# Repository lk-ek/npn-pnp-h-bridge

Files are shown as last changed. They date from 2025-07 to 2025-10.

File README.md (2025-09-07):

# H-Bridge Driver for 3.3V PWM Input (HI/LO)

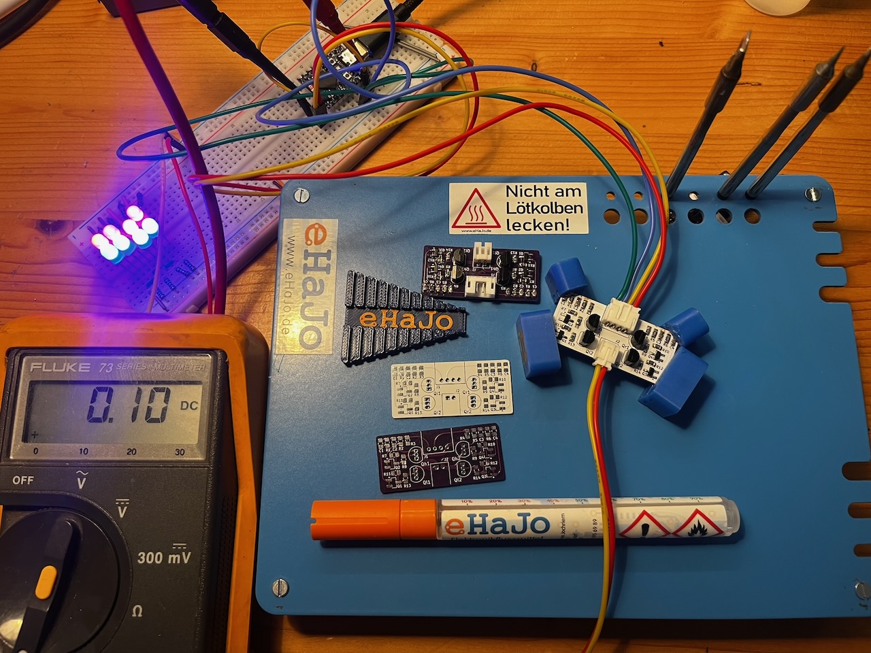
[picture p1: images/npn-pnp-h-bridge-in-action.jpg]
NPN-PNP-H-Bridge-in-action


This project is a discrete transistor-based H-bridge driver designed to drive loads such as a bi-directional LED string or small DC motors (you *need* to populate the protection diodes in that case!) using two 3.3V logic-level PWM inputs.

Special thanks to [PCBWay.com](https://pcbway.com) for reaching out to supply me with prototype PCBs. They turned out amazing and do work like a charm! This gave me the opportunity to fix a few things I got wrong in the first version - especially adding the protection diodes so this circuit can now not only drive LED-strips with anti-parallel circuits, but also small DC motors.

Also, if you are looking for a tool to handle your PCBs while soldering, look no further - [eHaJo's LötDock](https://www.ehajo.de/products/lotdock-workshop-set-a5-lotdock-base-a5-lotdock-starterkit) is there to save you! It's awesome. See it in action for a minute [here](https://www.youtube.com/watch?v=5W0FboXXDTc) (timelapse of the assembly of this PCB).

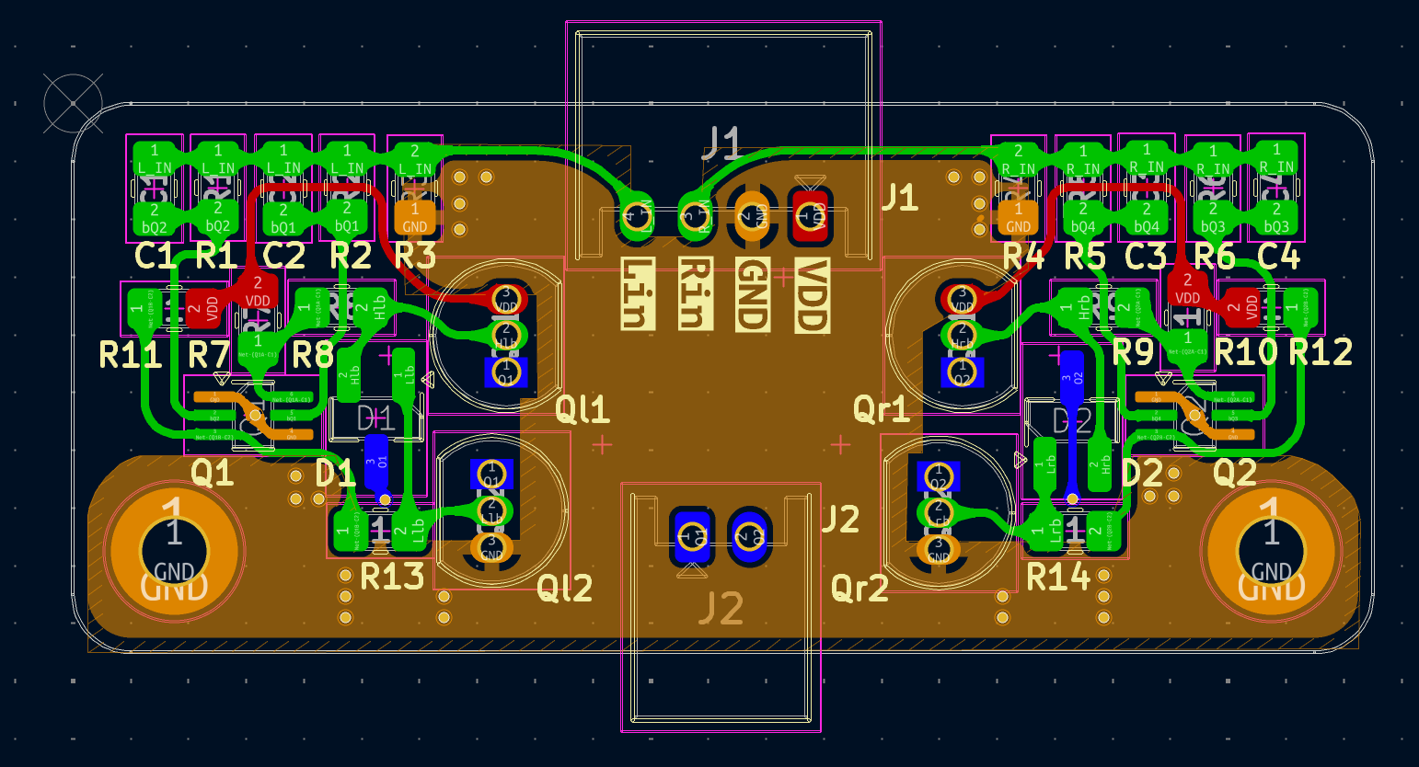
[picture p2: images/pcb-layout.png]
PCB Layout Front

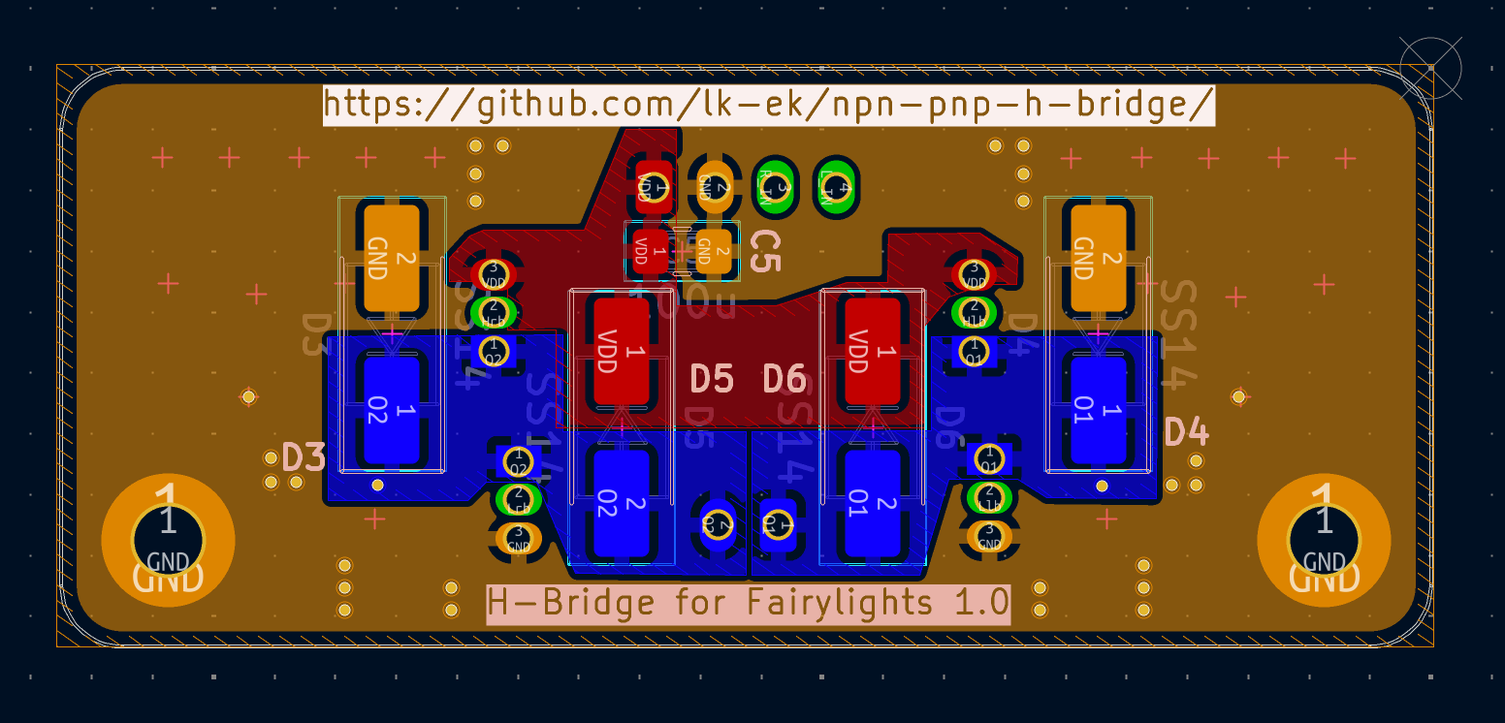
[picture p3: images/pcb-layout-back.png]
PCB Layout Back

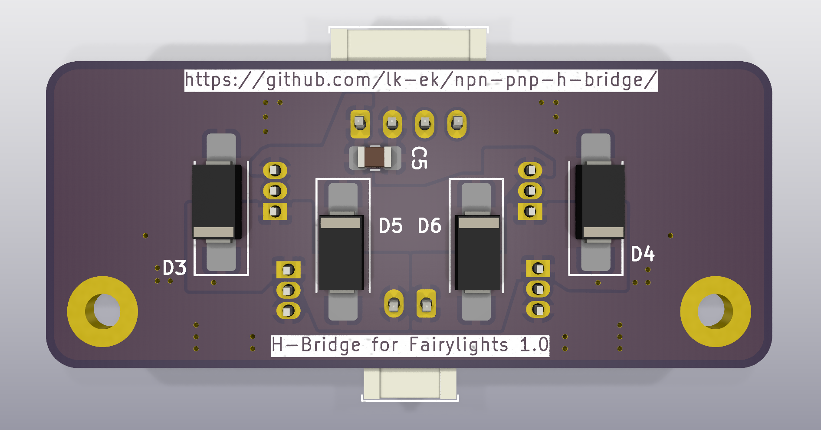
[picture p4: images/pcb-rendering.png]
PCB Rendering front

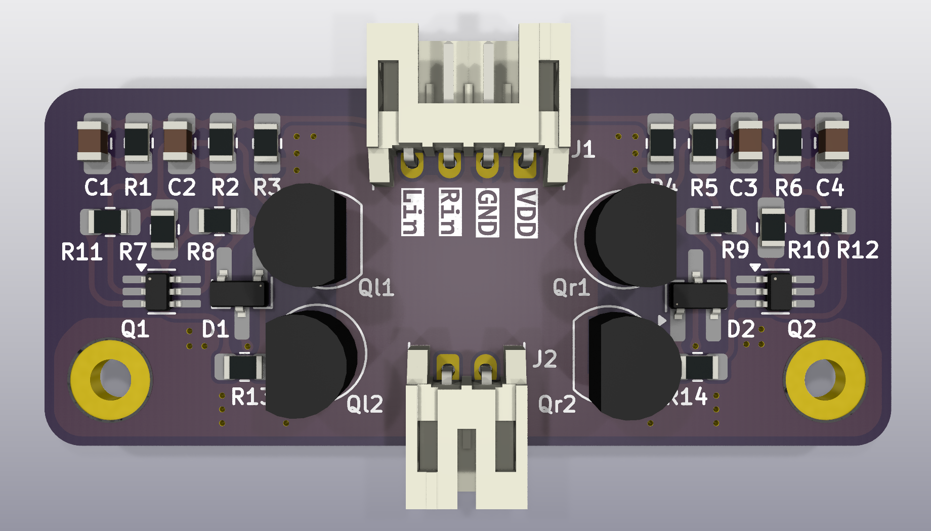
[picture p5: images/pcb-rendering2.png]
PCB Rendering back

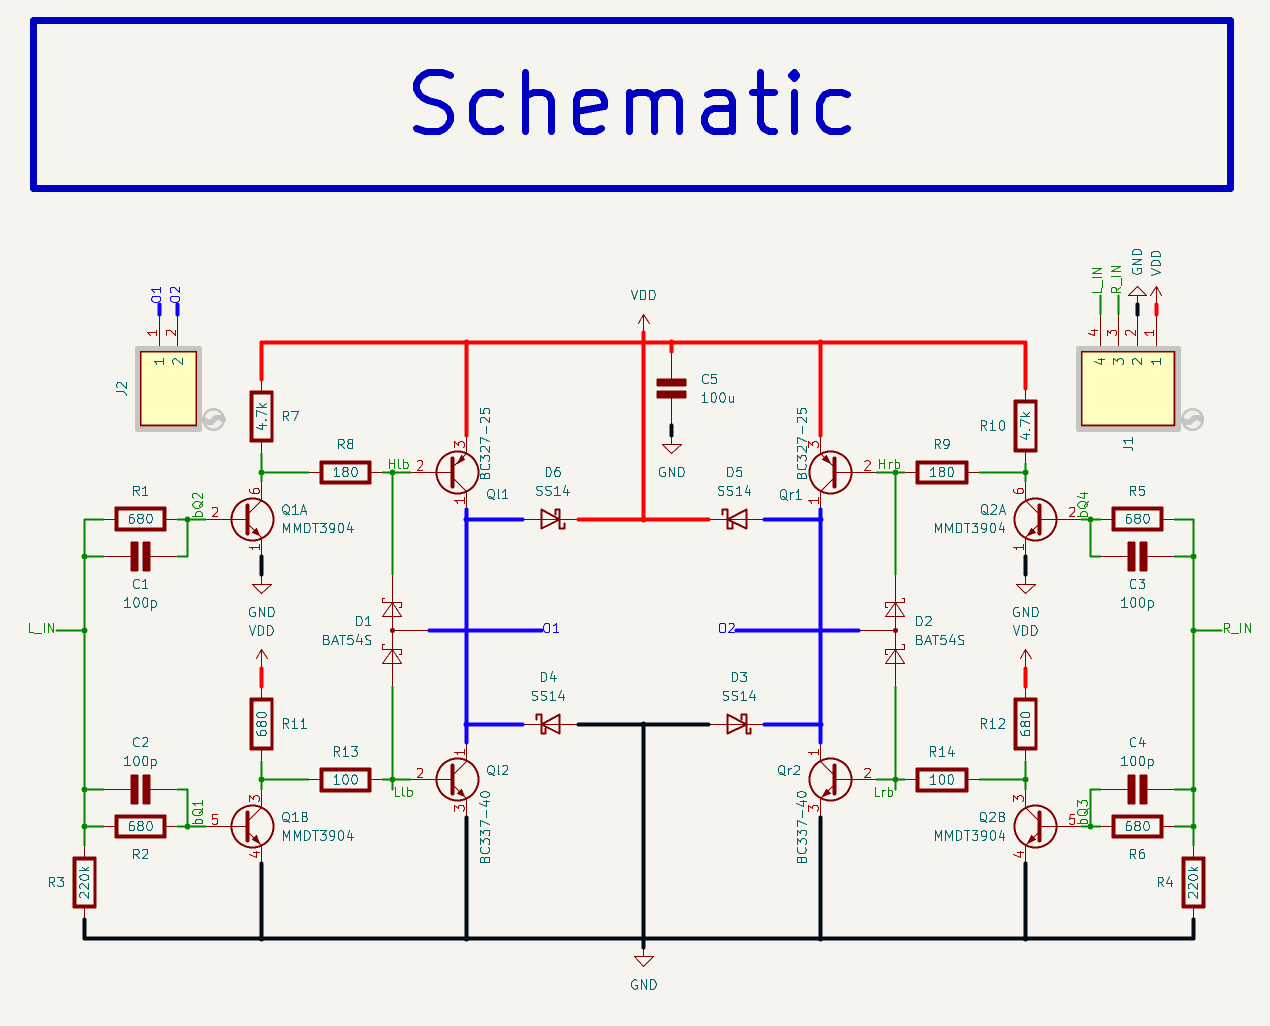
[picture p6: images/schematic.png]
Schematic


## Overview

The circuit takes two complementary (non-overlapping) PWM inputs: `L_IN` and `R_IN`, each at 3.3V logic level. These signals are level-shifted and drive a discrete H-bridge output stage composed of NPN and PNP BJTs. The output connects to a load (e.g., LED strip) in a push-pull fashion.

## Inputs

- `L_IN`: 3.3V logic PWM input (controls left-side NPN-PNP transistors)
- `R_IN`: 3.3V logic PWM input (controls right-side NPN-PNP transistors)

⚠️ **Important:**  
`L_IN` and `R_IN` **must be phase-shifted**, even though the NPN-PNP-pair makes sure shoot-through is impossible. If both are high simultaneously, the output is off.

## Supply

- `VDD`: Power rail for the H-bridge (used to drive the load), probably up to 12V
- `GND`: Common ground

## Outputs

- `O1`, `O2`: Differential outputs to the load

## Notes

- Input resistors and capacitors are used for filtering and protection.
- BJTs are used in complementary pairs (NPN/PNP) for each half-bridge.
- The BAT54S dual-diodes serve as a baker clamp to help the BJTs switch faster and reduce shoot-through from 2-3us to 0.5us in the simulation
- So far, a one-sided load of 210mA worked fine without anything getting noticably warm. In theory, it should tolerate at least 250mA on each side of the H-Bridge, so at least 500mA in total, but this is so far untested.
- Load: connected between `O1` and `O2` (e.g., antiparallel LEDs or small DC motor)
- You can use [WLED](https://kno.wled.ge/) to drive the inputs - select "PWM CCT" as LED-type. For the phase-shifted PWM to work, you might need to use a beta version from [wled-install.github.io](https://wled-install.github.io/) - 0.16 nightly worked for me.  
- [ESPHome](https://esphome.io) works as well, see example below

```yaml
output:
  - platform: ledc
    id: pwm_l
    pin: 3
    frequency: 5kHz
    inverted: false
    phase_angle: 0.0

  - platform: ledc
    id: pwm_r
    pin: 4
    frequency: 5kHz
    inverted: false
    phase_angle: 180.0

  - platform: template
    id: pwm_bridge
    type: float
    write_action:
      lambda: |-
        float duty = clamp(state, 0.0f, 1.0f) * 0.5f;
        id(pwm_l).set_level(duty);
        id(pwm_r).set_level(duty);
        ESP_LOGD("custom", "H-Bridge Control: L=%.2f R=%.2f", duty, duty);
light:
  - platform: monochromatic
    name: "Bidirektionale Lampe"
    output: pwm_bridge

```

## Simulation

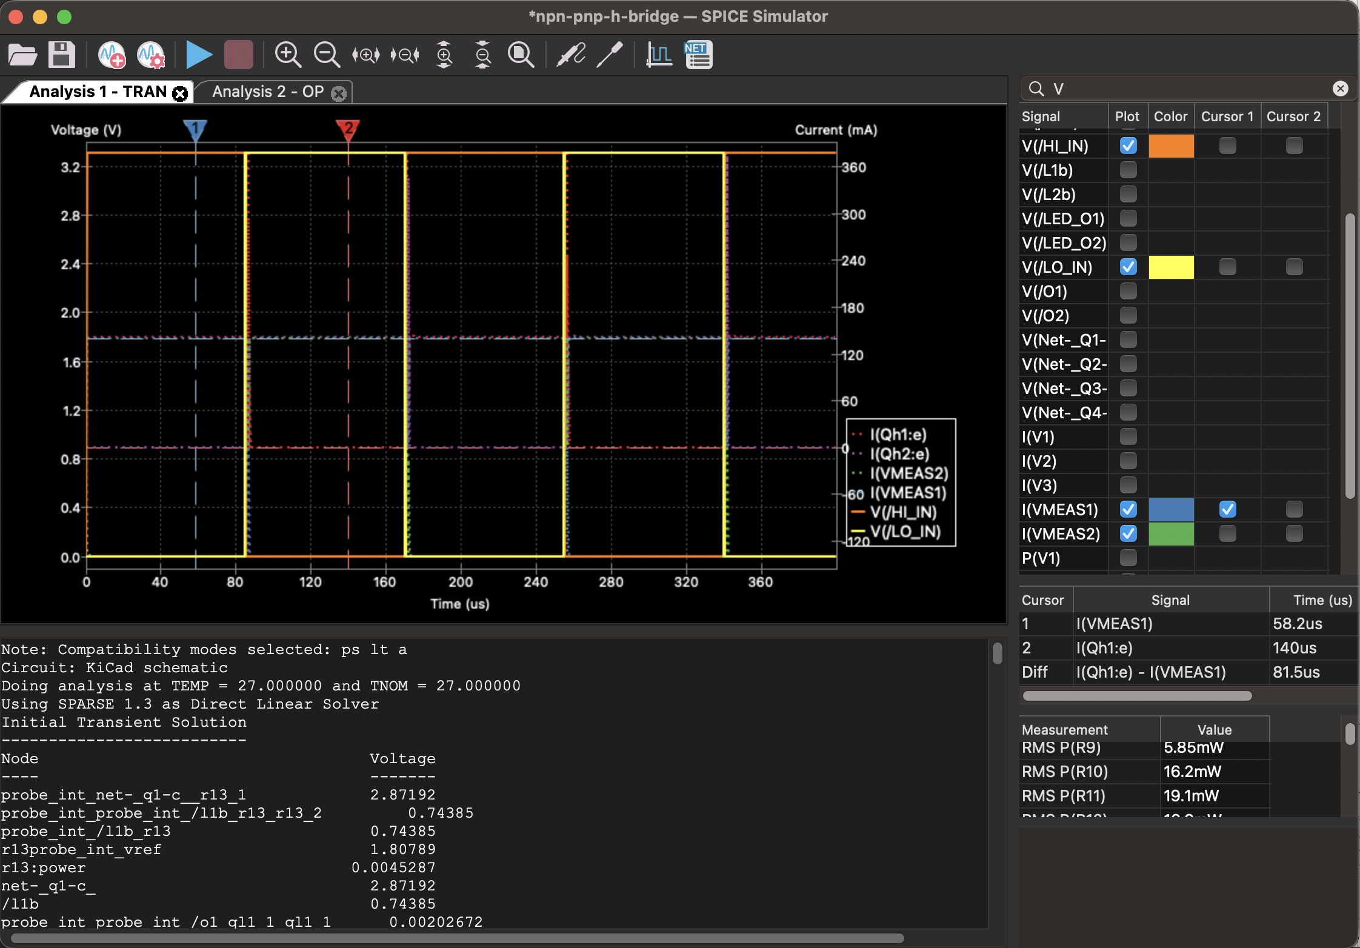
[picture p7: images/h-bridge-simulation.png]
H-Bridge Simulation

You can use KiCad's simulation tool to simulate the behaviour of this schematic. Modify the parameters of V1 and V2 to simulate different PWM patterns.

## Gerber files

You can download the gerber file directory as a zipfile and directly upload it to e.g. https://aisler.net, https://jlcpcb.com or https://pcbway.com

[Gerber file directory](production/npn-pnp-h-bridge)

## BOM

View [interactive BOM here](https://lk-ek.github.io/npn-pnp-h-bridge/)

| Designator | Amount | Value | Package |
|---|---|---|----|
| C1, C2, C3, C4 | 4 | 100p | 0805 
| C5 | 1 | 100u | 0805 
| D1, D2 | 2 | BAT54S Dual Schottky Diode | SOT-23 |
| D3, D4, D5, D6 | 4 | SS14 Schottky Diode | SMA |
| J1 | 1 | JST S4B-PH-K-S | JST PH 2.0mm |
| J2 | 1 | JST S2B-PH-K-S | JST PH 2.0mm |
| Q1, Q2 | 2 | MMDT3904 Dual NPN Package | SOT-363 |
| Ql1, Ql2 | 2 | BC327-25 | TO-92 |
| Qr1, Qr2 | 2 | BC337-40 | TO-92 |
| R1, R2, R5, R6, R11, R12 | 6 | 680 | 0805 |
| R3, R4 | 2 | 220k | 0805 |
| R7, R10 | 2 | 4.7k | 0805 |
| R8, R9 | 2 | 180 1/4W | 0805 |
| R13, R14 | 2 | 100 1/4W | 0805 |

## License

Attribution-NonCommercial-ShareAlike 4.0 International

See LICENSE for details, or: https://creativecommons.org/licenses/by-nc-sa/4.0/

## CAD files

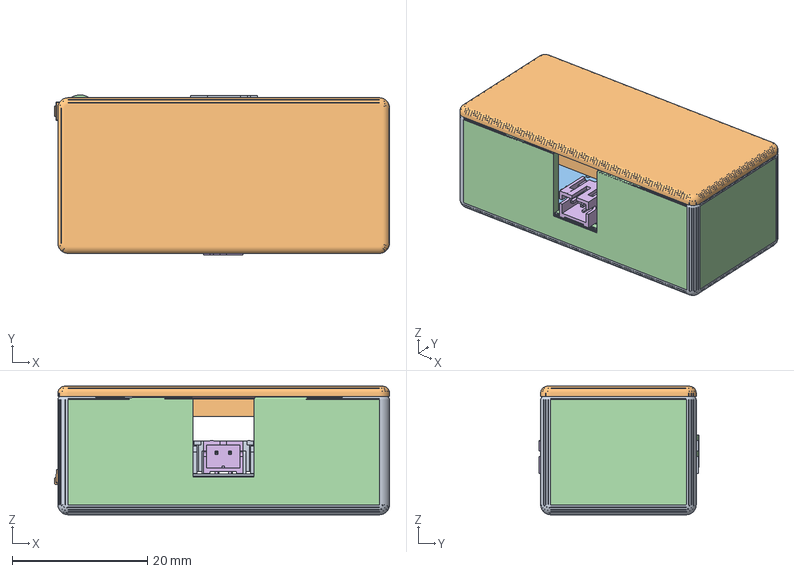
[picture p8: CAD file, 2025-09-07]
case/Test2.FCStd
49.5 x 23.7 x 19.0 mm
Deckel
C_0805_2012Metric
TO-92_Inline
R_0805_2012Metric
JST_PH_S2B-PH-K_1x02_P2.00mm_Horizontal
SOT-23
SOT-363_SC-70-6
JST_PH_S4B-PH-K_1x04_P2.00mm_Horizontal
D_SMA
npn-pnp-h-bridge_PCB
Body (Meshed)
Deckel (Meshed)

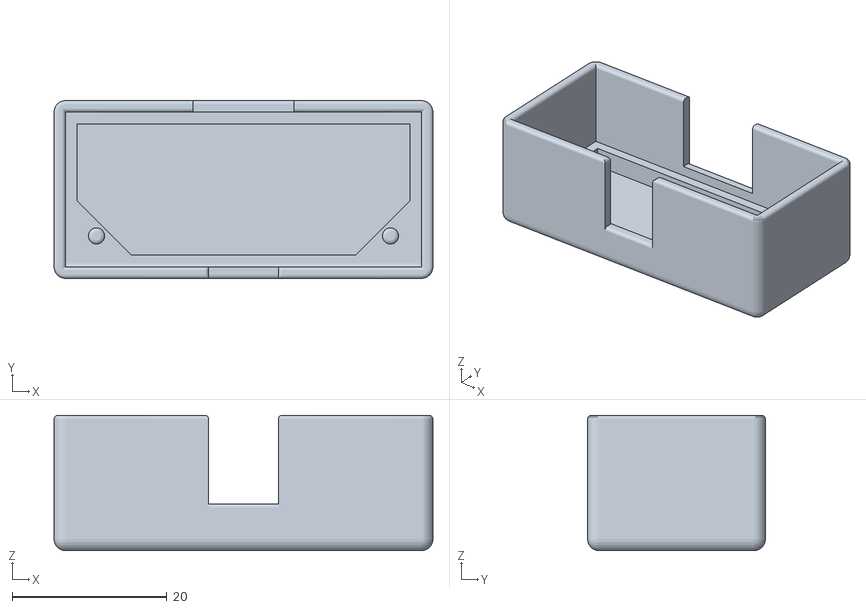
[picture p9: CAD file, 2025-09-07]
case/Body (Meshed).stl
49.0 x 23.0 x 17.5

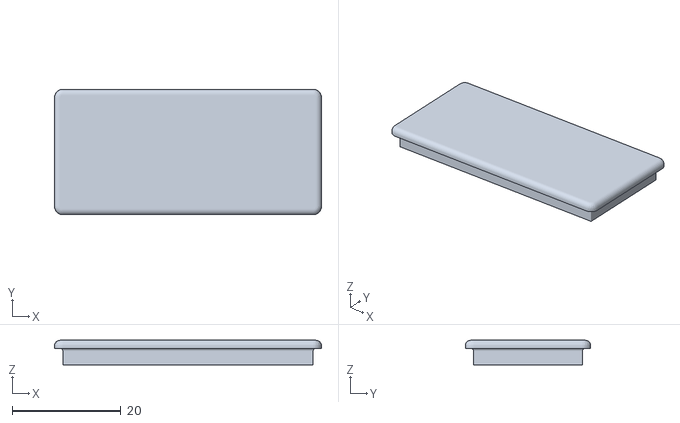
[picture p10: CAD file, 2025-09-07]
case/Deckel (Meshed).stl
49.0 x 23.0 x 4.50

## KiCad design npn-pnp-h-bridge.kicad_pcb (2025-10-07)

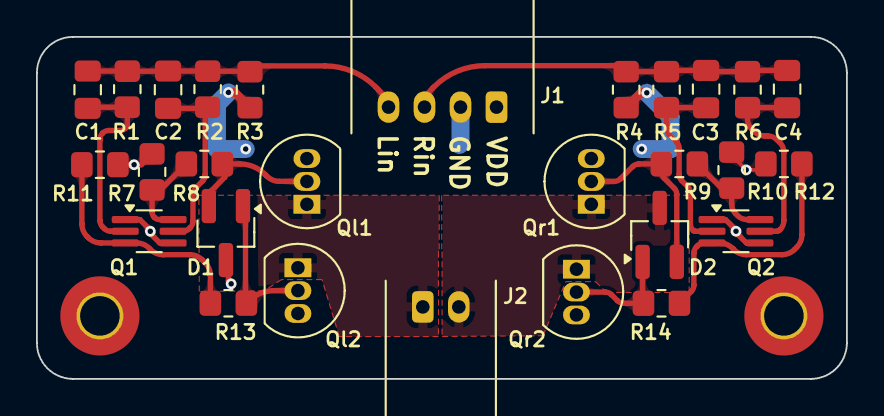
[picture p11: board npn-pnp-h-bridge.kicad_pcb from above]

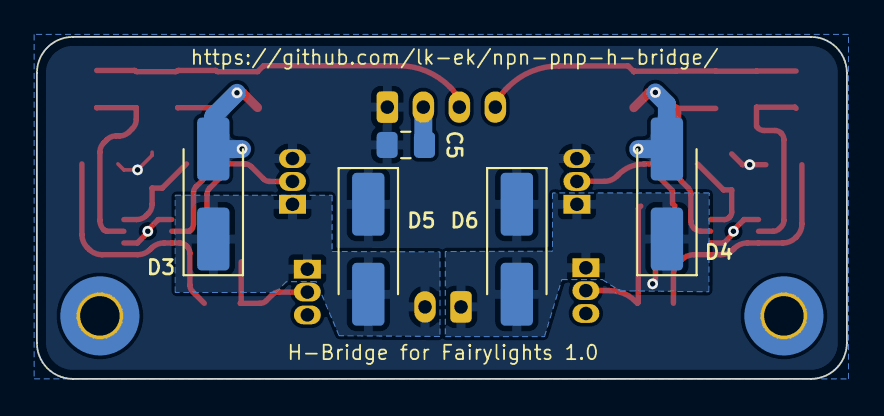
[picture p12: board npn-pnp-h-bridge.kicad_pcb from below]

Board: 4 copper layers, 45.0 x 19.0 mm, 35 parts (5 on the bottom side), 18 nets.

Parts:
C1, C2, C3, C4: 100p; C_0805_2012Metric_Pad1.18x1.45mm_HandSolder
C5: 100u; C_0805_2012Metric_Pad1.18x1.45mm_HandSolder
D1, D2: BAT54S; SOT-23_Handsoldering
D3, D4, D5, D6: SS14; D_SMA_Handsoldering
H1, H2: MountingHole_Pad; MountingHole_2.2mm_M2_Pad_TopBottom
J1: S4B-PH-K-S_LF__SN_; JST_PH_S4B-PH-K_1x04_P2.00mm_Horizontal
J2: S2B-PH-K-S_LF__SN_; JST_PH_S2B-PH-K_1x02_P2.00mm_Horizontal
Q1, Q2: MMDT3904; SOT-363_SC-70-6_Handsoldering
Ql1: BC327-25; TO-92_Inline
Ql2: BC337-40; TO-92_Inline
Qr1: BC327-25; TO-92_Inline
Qr2: BC337-40; TO-92_Inline
R1, R2, R5, R6: 680; R_0805_2012Metric_Pad1.20x1.40mm_HandSolder
R3, R4: 220k; R_0805_2012Metric_Pad1.20x1.40mm_HandSolder
R7, R10: 4.7k; R_0805_2012Metric_Pad1.20x1.40mm_HandSolder
R8, R9, R13, R14: 180; R_0805_2012Metric_Pad1.20x1.40mm_HandSolder
R11, R12: 2.2k; R_0805_2012Metric_Pad1.20x1.40mm_HandSolder

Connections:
/Hlb: D1.2 (K), Ql1.2 (B), R8.2 (-)
/Hrb: D2.2 (K), Qr1.2 (B), R9.1 (+)
/L_IN: C1.1 (+), C2.1 (+), J1.4, R1.1 (+), R2.1 (+), R3.2 (-)
/Llb: D1.1 (A), Ql2.2 (B), R13.2 (-)
/Lrb: D2.1 (A), Qr2.2 (B), R14.1 (+)
/O1: D1.3 (COM), D4.1 (K), D6.2 (A), J2.1, Ql1.1 (C), Ql2.1 (C)
/O2: D2.3 (COM), D3.1 (K), D5.2 (A), J2.2, Qr1.1 (C), Qr2.1 (C)
/R_IN: C3.1 (+), C4.1 (+), J1.3, R4.2 (-), R5.1 (+), R6.1 (+)
/bQ1: C2.2 (-), Q1.5 (B2), R2.2 (-)
/bQ2: C1.2 (-), Q1.2 (B1), R1.2 (-)
/bQ3: C4.2 (-), Q2.5 (B2), R6.2 (-)
/bQ4: C3.2 (-), Q2.2 (B1), R5.2 (-)
GND: C5.2 (-), D3.2 (A), D4.2 (A), H1.1, H2.1, J1.2, Q1.1 (E1), Q1.4 (E2), Q2.1 (E1), Q2.4 (E2), Ql2.3 (E), Qr2.3 (E), R3.1 (+), R4.1 (+)
unnamed: Q1.6 (C1), R7.1 (+), R8.1 (+)
unnamed: Q1.3 (C2), R11.1 (+), R13.1 (+)
unnamed: Q2.6 (C1), R9.2 (-), R10.1 (+)
unnamed: Q2.3 (C2), R12.1 (+), R14.2 (-)
VDD: C5.1 (+), D5.1 (K), D6.1 (K), J1.1, Ql1.3 (E), Qr1.3 (E), R7.2 (-), R10.2 (-), R11.2 (-), R12.2 (-)

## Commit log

2025-05-22 dont know what im doing
    [npn-pnp-h-bridge.kicad_sch]
2025-05-22 sort of working
    [npn-pnp-h-bridge.kicad_sch]
2025-05-22 sorta working
    [npn-pnp-h-bridge.kicad_sch]
2025-05-23 trying to reverse engineer original circuit
    [npn-pnp-h-bridge.kicad_sch]
2025-05-23 first appearently working prototype
    [npn-pnp-h-bridge.kicad_sch]
2025-05-23 change to bc807-40/817-40 and added mosfet to turn it all off
    [npn-pnp-h-bridge.kicad_sch]
2025-07-12 fillet PCB and change transistor footprints
    [npn-pnp-h-bridge.kicad_pcb, npn-pnp-h-bridge.kicad_sch]
2025-07-12 add spice models
    [npn-pnp-h-bridge.kicad_sch]
2025-07-12 add short BOM
2025-07-12 add package sizes to BOM
2025-07-12 replace images with current version; add schematic
2025-07-12 layout changes
    [npn-pnp-h-bridge.kicad_sch]
2025-07-12 cosmetic updates
    [npn-pnp-h-bridge.kicad_sch]
2025-07-12 add gerbers/fabrication output
    [npn-pnp-h-bridge-B_Cu.gbl, npn-pnp-h-bridge-B_Mask.gbs, npn-pnp-h-bridge-B_Paste.gbp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]
2025-07-12 describe gerber download
2025-07-21 colorful nets
    [npn-pnp-h-bridge.kicad_pcb, npn-pnp-h-bridge.kicad_sch]
2025-08-07 add iBOM
    [npn-pnp-h-bridge.kicad_sch]
2025-08-08 add optional freewheel diodes on the back layer
    [npn-pnp-h-bridge.kicad_pcb, npn-pnp-h-bridge.kicad_sch]
2025-08-08 update README for freewheel diodes
2025-08-08 add current gerbers and images
    [npn-pnp-h-bridge-B_Cu.gbl, npn-pnp-h-bridge-B_Mask.gbs, npn-pnp-h-bridge-B_Paste.gbp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]
2025-08-08 Thanks PCBWay for sponsoring prototypes of the new revision\!
    [npn-pnp-h-bridge-B_Cu.gbl, npn-pnp-h-bridge-B_Mask.gbs, npn-pnp-h-bridge-B_Paste.gbp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]
2025-08-22 Update README with current measurements; optimize resistor values for up to 500mA load
    [npn-pnp-h-bridge.kicad_pcb, npn-pnp-h-bridge.kicad_sch]
2025-08-22 update gerber files to current version
    [npn-pnp-h-bridge-B_Cu.gbl, npn-pnp-h-bridge-B_Mask.gbs, npn-pnp-h-bridge-B_Paste.gbp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]
2025-08-22 Add image from circuit in action
2025-08-22 Add PCBWay sponsoring and eHaJos LötDock
2025-08-24 tested with 210mA
2025-08-24 try adding a baker clamp
    [npn-pnp-h-bridge.kicad_sch]
2025-08-24 finish Baker-Clamp circuit and PCB. Reduces shoot-through in simulations from 2us to 0.5us.
    [npn-pnp-h-bridge-B_Cu.gbl, npn-pnp-h-bridge-B_Mask.gbs, npn-pnp-h-bridge-B_Paste.gbp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]
2025-08-24 add current images of baker-clamp version
2025-08-24 forgot C5 in BOM
2025-08-24 some small touchups
    [npn-pnp-h-bridge-B_Cu.gbl, npn-pnp-h-bridge-B_Mask.gbs, npn-pnp-h-bridge-B_Paste.gbp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]
2025-08-24 Use handsoldering-footprints for diodes
    [npn-pnp-h-bridge-B_Cu.gbl, npn-pnp-h-bridge-B_Mask.gbs, npn-pnp-h-bridge-B_Paste.gbp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]
2025-08-24 add baker clamp to README.md
2025-08-24 beautify schematic
    [npn-pnp-h-bridge.kicad_pcb, npn-pnp-h-bridge.kicad_sch]
2025-08-24 Changed MMBT3904 for a dual-NPN MMDT3904 for miniturization
    [npn-pnp-h-bridge-B_Cu.gbl, npn-pnp-h-bridge-B_Mask.gbs, npn-pnp-h-bridge-B_Paste.gbp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]
2025-08-24 update BOM
2025-08-24 fine tuning
    [npn-pnp-h-bridge-B_Cu.gbl, npn-pnp-h-bridge-B_Mask.gbs, npn-pnp-h-bridge-B_Paste.gbp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]
2025-08-24 more fine tuning; round board size
    [npn-pnp-h-bridge-B_Cu.gbl, npn-pnp-h-bridge-B_Mask.gbs, npn-pnp-h-bridge-B_Paste.gbp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]
2025-08-26 final touches for dual-npn-package
    [npn-pnp-h-bridge-B_Cu.gbl, npn-pnp-h-bridge-B_Mask.gbs, npn-pnp-h-bridge-B_Paste.gbp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]
2025-08-29 Add experimental and untested 3d model for a case
    [Test2-Body.stl, Test2-Deckel.stl, Test2.FCStd]
2025-08-31 pushed out the connectors to match the case
    [Test2.FCStd, npn-pnp-h-bridge.kicad_pcb, npn-pnp-h-bridge.kicad_sch]
2025-09-07 Add 1.0 revision number, use current screenshots, add exported case
    [Body (Meshed).stl, Deckel (Meshed).stl, Test2.FCStd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]
2025-09-10 changed some resistor values back to old values since the BJTs got very hot with lower pullups and lower base resistors
    [npn-pnp-h-bridge.kicad_sch]
2025-09-10 update pcb with new values
    [npn-pnp-h-bridge.kicad_pcb]
2025-10-03 first 4-layer try
    [npn-pnp-h-bridge.kicad_pcb]
2025-10-07 finalize 4-layer design
    [npn-pnp-h-bridge.kicad_pcb]
